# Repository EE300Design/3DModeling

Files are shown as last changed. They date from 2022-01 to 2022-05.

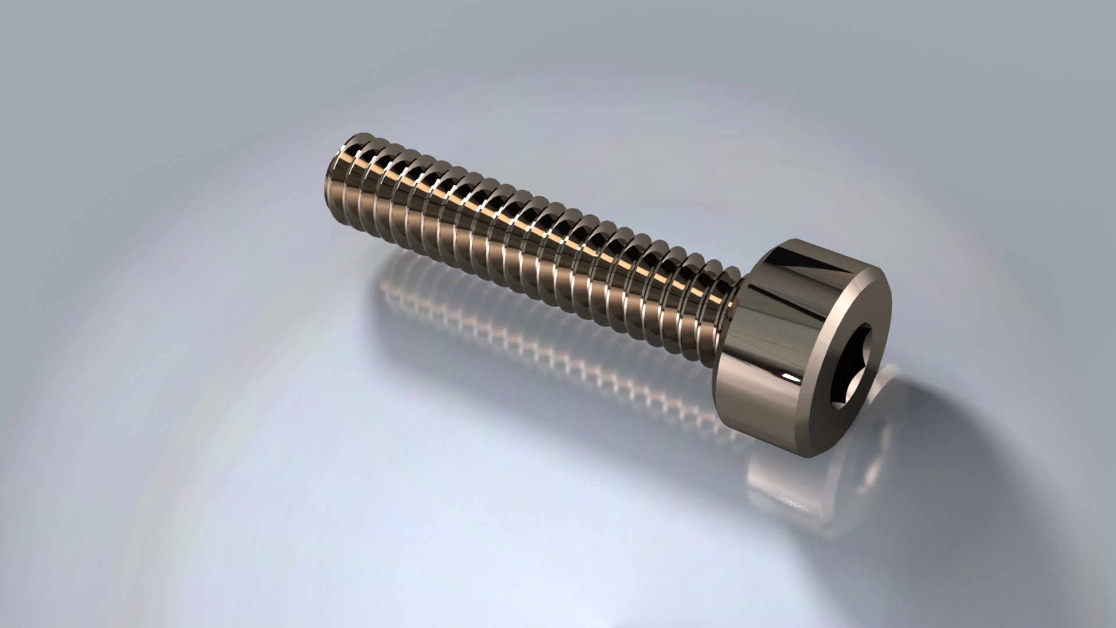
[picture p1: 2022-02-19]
Fusion_Model/Component_Models/M2_Metric_Screws/all-m2-sh-standard-screws-m2-hex-nut-and-flat-washer-for-m2-screw-1.snapshot.20/Metric Screw (3) 2.jpg

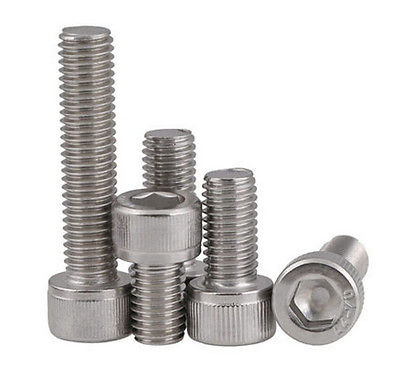
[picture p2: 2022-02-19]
Fusion_Model/Component_Models/M2_Metric_Screws/all-m2-sh-standard-screws-m2-hex-nut-and-flat-washer-for-m2-screw-1.snapshot.20/M2-M25-M3-316-A4-Stainless-Steel-Hex.jpg

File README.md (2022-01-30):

# 3DModeling
This is the working space for EE300 design project collaboration

## References
[1] https://lidarscanner.wordpress.com/2015/03/28/final-presentation/ \
[2] https://cdn.webshopapp.com/shops/304271/files/333438293/develop-routine-of-tf-luna-in-arduino.pdf \
[3] https://github.com/budryerson/TFLuna-I2C \
[4] https://youtu.be/diuOMDRtIMI \
[5] https://github.com/TravisLedo/LidarScanRender \
[6] https://create.arduino.cc/projecthub/TravisLedo/arduino-lidar-scanning-java-rendering-6b2124 \
[7] https://www.arduino.cc/reference/en/libraries/stepperdriver/ \
[8] https://www.youtube.com/watch?v=fHAO7SW-SZI

## Parts
| Component | Quantity | Purpose | Link | Cost($) |
| --- | --- | --- | --- | --- |
| `Nema17 Stepper Motor` | 1 | Drive Rotation Plate | https://www.amazon.com/dp/B07THK76QQ?psc=1&ref=ppx_yo2_dt_b_product_details | 10.99 |
| `Nema17 Stepper Motor 400mm thread` | 1 | Vertical Motion | https://www.amazon.com/dp/B07YQQGQ4C?psc=1&ref=ppx_yo2_dt_b_product_details | 35.99 |
| `450mm Linear Motion Rails` | 4 | Vertical Motion Support | https://www.amazon.com/dp/B08HWJVX63?psc=1&ref=ppx_yo2_dt_b_product_details | 35.98 |
| `12mm Linear Ball Bearing` | 4 | Vertical Motion | https://www.amazon.com/dp/B07H95FFP1?ref=ppx_yo2_dt_b_product_details&th=1 | 11.99 |
| `TF-Luna Lidar` | 1 | LIDAR | https://www.amazon.com/dp/B08F55QTWP?psc=1&ref=ppx_yo2_dt_b_product_details |25.98 |
| `A4988 Stepper Driver` | 5 | Stepper Driver | https://www.amazon.com/dp/B07BND65C8?psc=1&ref=ppx_yo2_dt_b_product_details | 9.69 |
| `Arduino Uno R3` | 1 | Micro-Controller | https://www.amazon.com/dp/B008GRTSV6?psc=1&ref=ppx_yo2_dt_b_product_details | 22.88 |
| `Nylon Spacer` | 320 | PCB Stand-off | https://www.amazon.com/dp/B008GRTSV6?psc=1&ref=ppx_yo2_dt_b_product_details | 11.88 |
| `M3 Threaded Inserts` | 120 | PCB Mounting | https://www.amazon.com/dp/B09KZSJS88?psc=1&ref=ppx_yo2_dt_b_product_details | 12.99 |
| `100uF Cap` | 20 | PCB | https://www.digikey.com/en/products/detail/kemet/ESK107M016AE3AA/13176338 | 3.42 | 
| `0.1uF Cap` | 20 | PCB | https://www.digikey.com/en/products/detail/w%C3%BCrth-elektronik/885012207045/5453900 | 1.12 |
| `TE 1x4 Connector`| 4 | PCB | https://www.digikey.com/en/products/detail/te-connectivity-amp-connectors/796949-4/2223910 | 8.12 |
| `PWR Jack` | 4 | PCB | https://www.digikey.com/en/products/detail/te-connectivity-amp-connectors/796949-4/2223910 | 2.76 |

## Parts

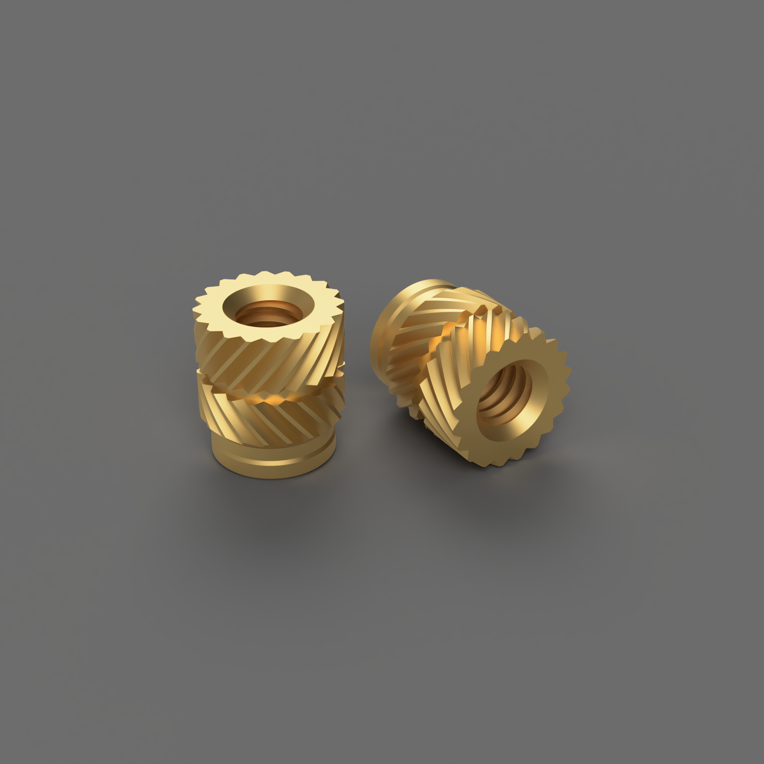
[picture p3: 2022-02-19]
Fusion_Model/Component_Models/M2_Threaded_Insert/threaded-insert-m2-x-4mm-for-3d-printed-parts-1.snapshot.5/08a98328-2d2f-4b6d-87d2-8571cb3f2b7b 2.PNG

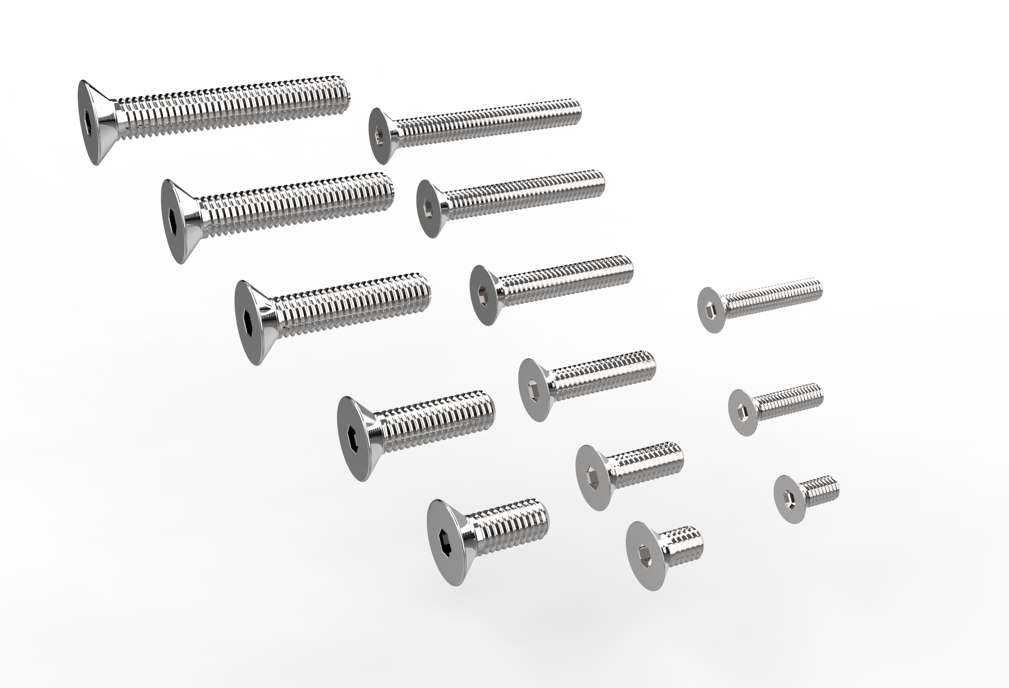
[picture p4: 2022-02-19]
Fusion_Model/Component_Models/Metric_Screws/All_Screws_M3_M4_M5/untitled.126.png

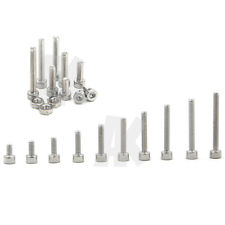
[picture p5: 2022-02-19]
Fusion_Model/Component_Models/M2_Metric_Screws/all-m2-sh-standard-screws-m2-hex-nut-and-flat-washer-for-m2-screw-1.snapshot.20/s-l225 2.jpg

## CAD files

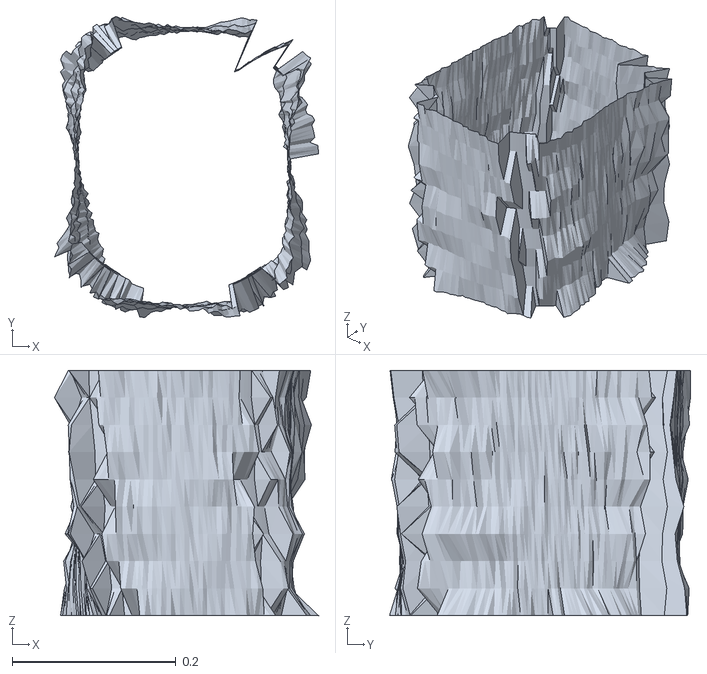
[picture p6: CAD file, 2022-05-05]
Application/Saved_examples/First_cube.stl
0.323 x 0.368 x 0.3

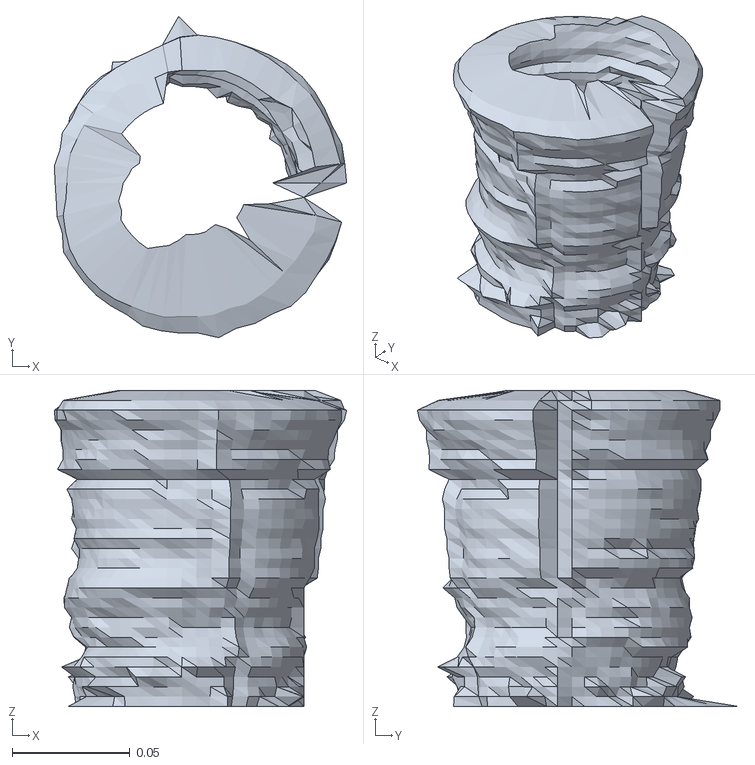
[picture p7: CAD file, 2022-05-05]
Application/test.stl
0.124 x 0.137 x 0.134

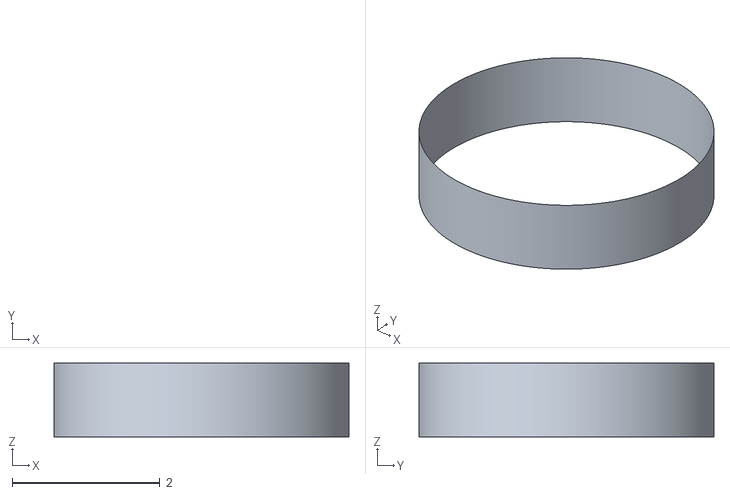
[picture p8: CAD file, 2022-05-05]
data_processing/test.stl
4.00 x 4.00 x 1.00

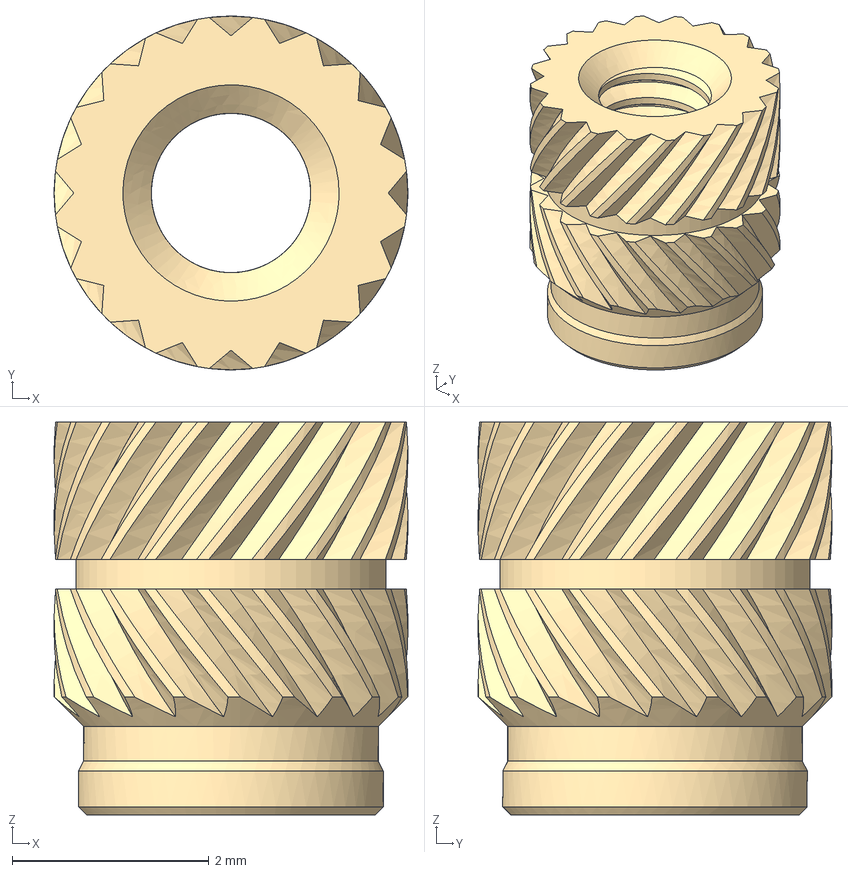
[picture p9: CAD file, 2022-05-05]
Fusion_Model/Component_Models/M2_Threaded_Insert/threaded-insert-m2-x-4mm-for-3d-printed-parts-1.snapshot.5/Threaded Insert M2 v1.iges
3.60 x 3.60 x 4.00 mm

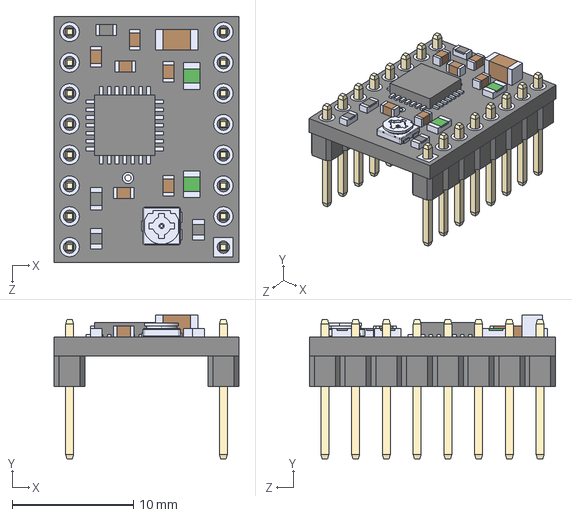
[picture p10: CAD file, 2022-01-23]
PCB_Design/Libraries&Footprints/A4988_Stepper_Driver/A4988_STEPPER_MOTOR_DRIVER_CARRIER.step
15.2 x 11.9 x 20.3 mm

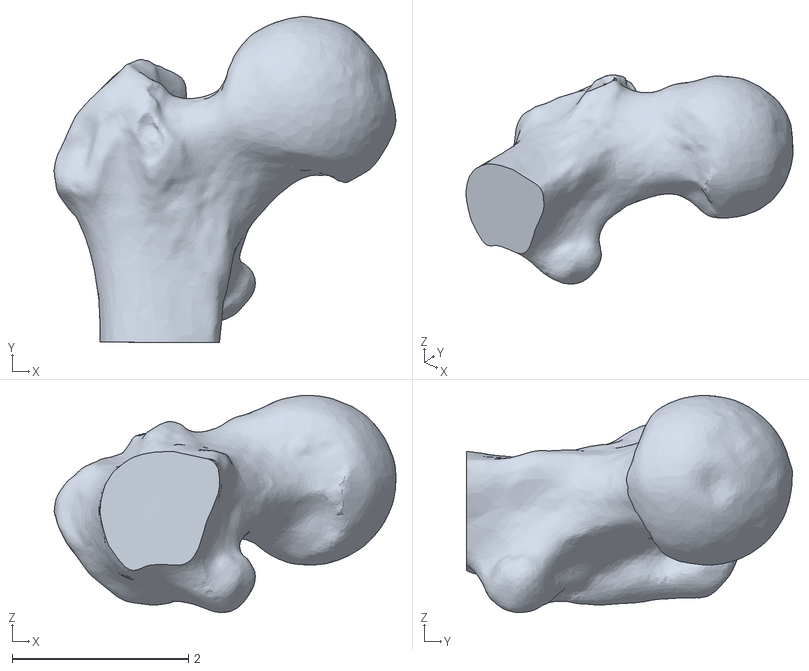
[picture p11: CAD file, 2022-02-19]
Application/femur.stl
3.87 x 3.70 x 2.46

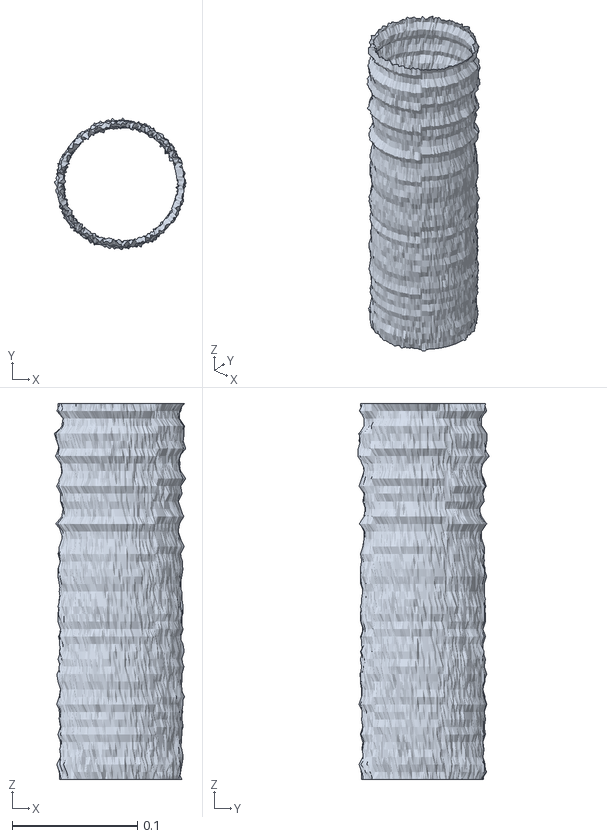
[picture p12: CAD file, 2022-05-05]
Application/Saved_examples/Oats_can.stl
0.105 x 0.105 x 0.3

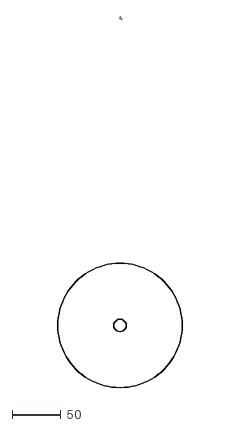
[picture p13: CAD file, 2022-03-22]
Fusion_Model/3D_STLS/Plate_DXF.dxf
128.0 x 382.2

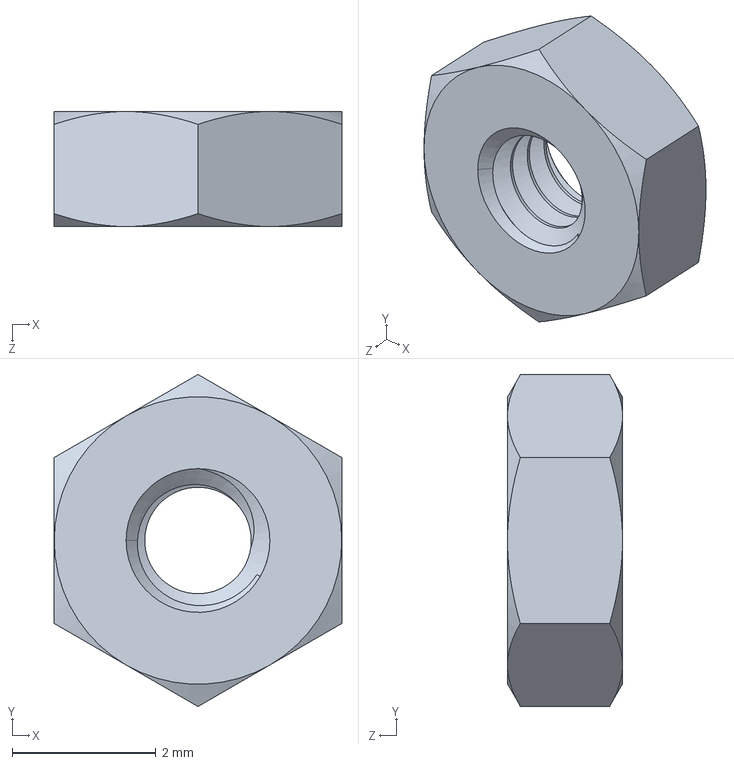
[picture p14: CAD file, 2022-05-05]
Fusion_Model/Component_Models/M2_Metric_Screws/all-m2-sh-standard-screws-m2-hex-nut-and-flat-washer-for-m2-screw-1.snapshot.20/M2 x 0.4mm Thread HEX NUT 2.STEP
4.00 x 4.62 x 1.60 mm

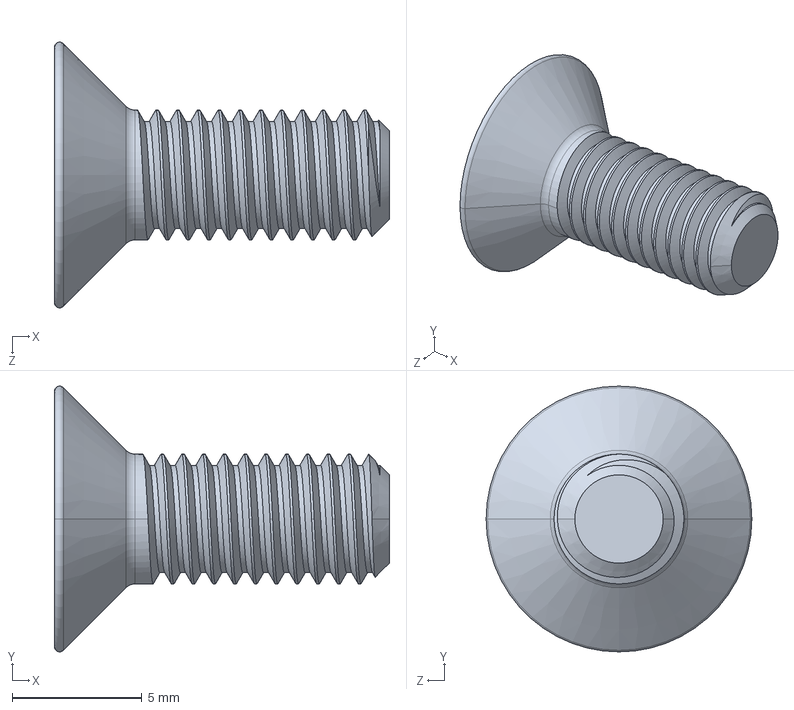
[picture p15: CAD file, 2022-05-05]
Fusion_Model/Component_Models/Metric_Screws/All_Screws_M3_M4_M5/M5_Countersunk_10 2.STEP
12.9 x 10.2 x 10.2 mm

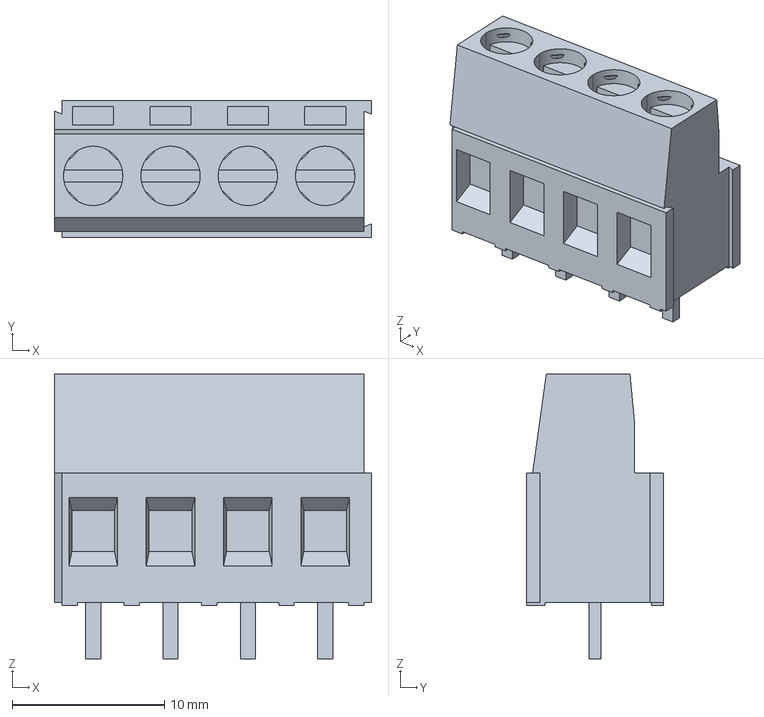
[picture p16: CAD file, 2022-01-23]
PCB_Design/Libraries&Footprints/TE_Terminal_Block/796949-4.step
20.8 x 9.00 x 18.7 mm

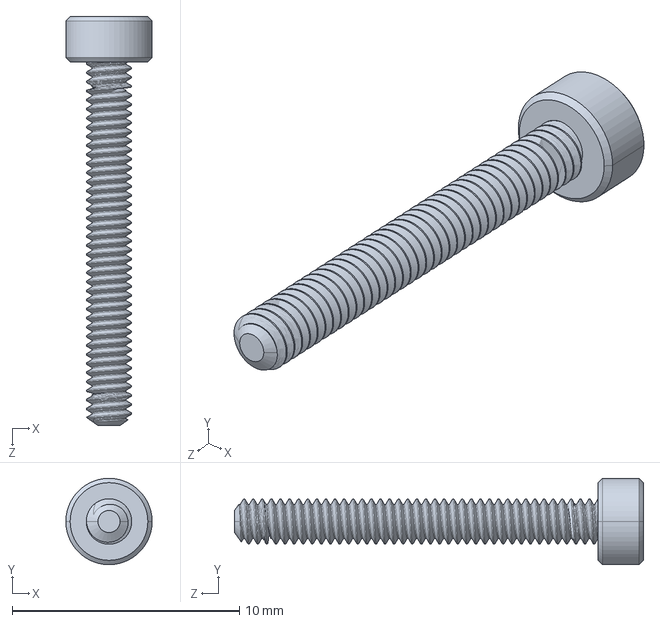
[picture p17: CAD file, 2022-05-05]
Fusion_Model/Component_Models/M2_Metric_Screws/all-m2-sh-standard-screws-m2-hex-nut-and-flat-washer-for-m2-screw-1.snapshot.20/M2 x 0.4mm Thread 16mm LONG SOCKET HEAD CAP SCREW.STEP
3.80 x 3.80 x 18.0 mm

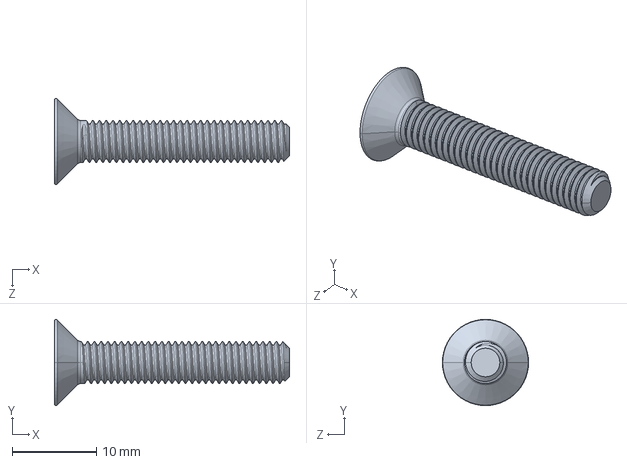
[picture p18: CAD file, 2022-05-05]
Fusion_Model/Component_Models/Metric_Screws/All_Screws_M3_M4_M5/M5_Countersunk_25 2.STEP
27.9 x 10.2 x 10.2 mm

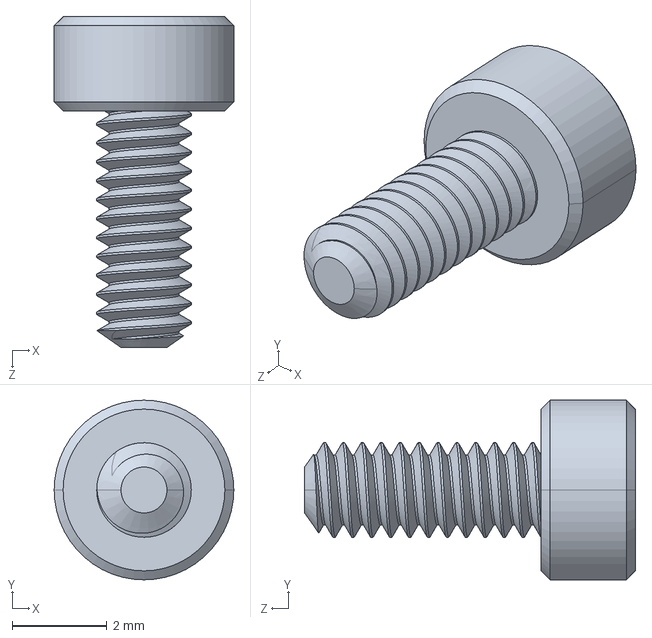
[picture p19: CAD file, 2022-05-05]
Fusion_Model/Component_Models/M2_Metric_Screws/all-m2-sh-standard-screws-m2-hex-nut-and-flat-washer-for-m2-screw-1.snapshot.20/M2 x 0.4mm Thread 5mm LONG SOCKET HEAD CAP SCREW.STEP
3.80 x 3.80 x 7.00 mm

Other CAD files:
Fusion_Model/3D_STLS/Plate_DXF_recover.dwg
Fusion_Model/Component_Models/Metric_Screws/All_Screws_M3_M4_M5/M4_Counter_sunk_20 2.STEP
Fusion_Model/Component_Models/M2_Metric_Screws/all-m2-sh-standard-screws-m2-hex-nut-and-flat-washer-for-m2-screw-1.snapshot.20/M2 x 0.4mm Thread 6mm LONG SOCKET HEAD CAP SCREW 2.STEP
Fusion_Model/Component_Models/M2_Metric_Screws/all-m2-sh-standard-screws-m2-hex-nut-and-flat-washer-for-m2-screw-1.snapshot.20/M2 screw size FLAT WASHER 2.STEP
Fusion_Model/Component_Models/M2_Metric_Screws/all-m2-sh-standard-screws-m2-hex-nut-and-flat-washer-for-m2-screw-1.snapshot.20/M2 screw size FLAT WASHER 2.x_t
Fusion_Model/Component_Models/M2_Metric_Screws/all-m2-sh-standard-screws-m2-hex-nut-and-flat-washer-for-m2-screw-1.snapshot.20/M2 screw size FLAT WASHER.STEP
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

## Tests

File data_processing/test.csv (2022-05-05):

2.000000000000000000e+00 | 2.000000000000000000e+00 | 2.000000000000000000e+00 | 2.000000000000000000e+00 | 2.000000000000000000e+00 | 2.000000000000000000e+00 | 2.000000000000000000e+00 | 2.000000000000000000e+00 | 2.000000000000000000e+00 | 2.000000000000000000e+00 | 2.000000000000000000e+00 | 2.000000000000000000e+00 | 2.000000000000000000e+00 | 2.000000000000000000e+00 | 2.000000000000000000e+00 | 2.000000000000000000e+00 | 2.000000000000000000e+00 | 2.000000000000000000e+00 | 2.000000000000000000e+00 | 2.000000000000000000e+00 | 2.000000000000000000e+00 | 2.000000000000000000e+00 | 2.000000000000000000e+00 | 2.000000000000000000e+00 | 2.000000000000000000e+00 | 2.000000000000000000e+00 | 2.000000000000000000e+00 | 2.000000000000000000e+00 | 2.000000000000000000e+00 | 2.000000000000000000e+00 | 2.000000000000000000e+00 | 2.000000000000000000e+00 | 2.000000000000000000e+00 | 2.000000000000000000e+00 | 2.000000000000000000e+00 | 2.000000000000000000e+00 | 2.000000000000000000e+00 | 2.000000000000000000e+00 | 2.000000000000000000e+00 | 2.000000000000000000e+00 | 2.000000000000000000e+00 | 2.000000000000000000e+00 | 2.000000000000000000e+00 | 2.000000000000000000e+00 |
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

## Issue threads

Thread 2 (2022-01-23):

Sourced Parts

LixianY, 2022-01-23:
Order the basic parts for the scanning platform construction.
These parts are :
1.Microcontroller:
https://www.amazon.com/Arduino-A000066-ARDUINO-UNO-R3/dp/B008GRTSV6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

2.Linear Rails for Stepper & Vertical Climb x4(450mm);
https://www.amazon.com/Linear-Motion-Hardened-Printer-Tolerance/dp/B08HWJVX63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

3.Nema17 Stepper Motor 400MM threaded:
https://www.amazon.com/Iverntech-Stepper-Integrated-Printers-Machine/dp/B07YQQGQ4C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

4.AR4988 Driver:
https://www.amazon.com/HiLetgo-Stepstick-Stepper-Printer-Compatible/dp/B07BND65C8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

5.LiDAR sensor:
https://www.amazon.com/gp/product/B088BBJ9SQ/ref=ox_sc_act_title_2?smid=AIJ7WJJN4HG6E&psc=1

Closed 2022-02-06.

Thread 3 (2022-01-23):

Search learning sources for 3D modeling

LixianY, 2022-01-23:
Find articles or blogs about:

1. Controlling the stepper motor.
2. Software platform for presenting 3D cloud dots collected by LiDAR sensors.
3. Needed mathetical tutorials, like coordinate transformation.

Closed 2022-04-23.

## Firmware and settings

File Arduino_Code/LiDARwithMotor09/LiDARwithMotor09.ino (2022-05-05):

#include <SoftwareSerial.h> //header file of software serial port
//The next line is commented as we are using mega
//SoftwareSerial Serial1(7,8); //define software serial port name as Serial1 and define pin7 as RX and pin8 as TX

//This version deals with limiting switches

/* For Arduino boards with multiple serial ports like DUEboard, interpret the above two pieces of code and directly use Serial1 serial port*/
int dist; //actual distance measurements of LiDAR 
int strength; //signal strength of LiDAR
float x_cor;
float y_cor;

//////////////////////////////
int check; //save check value
int i;
int uart[9]; //save data measured by LiDAR
const int HEADER=0x59; //frame header of data package 

// defines pins numbers
// Disk rotation motor
const int stepPin1 = 3; 
const int dirPin1 = 4; 
// Screw rotation motor
const int stepPin2 = 5; 
const int dirPin2 = 6; 
// Set up for limiting switches
const int LimSwitchUp = 8;
const int LimSwitchDw = 9;

const int heightIncrement = 80; // Height increment amount after one disk rotation


void setup() {
  Serial.begin(9600); //set bit rate of serial port connecting Arduino with computer
  Serial1.begin(115200); //set bit rate of serial port connecting LiDAR with Arduino 
    // For Stepper Motors, sets the four pins as Outputs
  pinMode(stepPin1,OUTPUT); // Disk rotation motor
  pinMode(dirPin1,OUTPUT);
  pinMode(stepPin2,OUTPUT); // Screw rotation motor
  pinMode(dirPin2,OUTPUT);
  pinMode(7,INPUT);// interrupt button
  pinMode(LimSwitchUp, INPUT);
  pinMode(LimSwitchDw, INPUT);
}


float heightData = 0;
int h = 0;
const int Length = 47; //sensor to the center of disk distance in cm


///////////////


void stop_scan(){
  digitalWrite(dirPin1,LOW); // Set the motor pins to a fixed value to stop them
  digitalWrite(stepPin1,HIGH); 
  digitalWrite(dirPin2,LOW); //
  digitalWrite(stepPin2,HIGH); 
  //digitalWrite(7,LOW);
  // Later, need to record the index where it stopped so that it can properly resume.
  
  }





void start_scan()//
{
  delay(100);
  bool exit_scan=false;
    //Set scanning max height limit 360 is found by 7200steps/20
  while(!exit_scan) {
    
    float theta = 0; // Angle of the disk rotation
    digitalWrite(dirPin1,LOW); // Enables the motor to move in a particular direction
    // Makes 200 pulses for making one full cycle rotation
    for(int x = 0; x < 200;) {
     int UpLim = digitalRead(LimSwitchUp);
     int DwLim = digitalRead(LimSwitchDw);
     int interrupt = digitalRead(7);
     
     if(interrupt == HIGH){
      
       stop_scan();
       digitalWrite(11,interrupt);
       exit_scan = true;
       break;
      }

      //Check if the upper limiting switch is pressed
      
      if(UpLim == HIGH){
        Serial.println("Move Down");
        digitalWrite(dirPin2,HIGH);
        
        //If pressed, rotates the carriage downward till initial position
        while(DwLim == LOW){
        DwLim = digitalRead(LimSwitchDw);
        digitalWrite(stepPin2,HIGH); 
        delayMicroseconds(500); 
        digitalWrite(stepPin2,LOW); 
        delayMicroseconds(500);
        }
        exit_scan = true;
        break;
        }
     
     if (Serial1.available()) { //check if serial port has data input
        if(Serial1.read() == HEADER) { //assess data package frame header 0x59 
          uart[0]=HEADER;
            if (Serial1.read() == HEADER) { //assess data package frame header 0x59
              uart[1] = HEADER;
              for (i = 2; i < 9; i++) { //save data in array
                uart[i] = Serial1.read(); 
                }
              check = uart[0] + uart[1] + uart[2] + uart[3] + uart[4] + uart[5] + uart[6] + uart[7]; 
              if (uart[8] == (check & 0xff)) { //verify the received data as per protocol
                dist = uart[2] + uart[3] * 256; //calculate distance value [mm]
                float cmdist = dist/10.0;  // convert to cm
                strength = uart[4] + uart[5] * 256; //calculate signal strength value 
          
                //Serial1.flush();
                delay(100);
                digitalWrite(stepPin1,HIGH); 
                delayMicroseconds(100); 
                digitalWrite(stepPin1,LOW); 
                delayMicroseconds(100);
                theta += 1.8;

                x++;
                // check if one full rotation completed
                if (x==200){
                  digitalWrite(dirPin2,LOW); // Enables the motor to move in clockwise direction
                                             // Makes 200 pulses for making one full cycle rotation
 
                  for(int x = 0; x < heightIncrement; x++) {
                      digitalWrite(stepPin2,HIGH); 
                      delayMicroseconds(500); 
                      digitalWrite(stepPin2,LOW); 
                      delayMicroseconds(500); 
                    }
    
                  h += heightIncrement; // counting height rotation steps
                  heightData = (heightData + h/26.7)/10; // calculate the hieght in cm
                  }

                // Perform coordinate conversion  
//                Serial.print(cmdist);
//                Serial.print(' ');
                x_cor = (Length-cmdist)*cos((theta/180) * 3.14159);
                y_cor = (Length-cmdist)*sin((theta/180) * 3.14159);
                Serial.print(x_cor); // output disk rotation angle
                Serial.print(' ');
                Serial.print(y_cor);
                Serial.print(' ');
                Serial.println(heightData);
               
                
          } 
         }
       }
    }
    else{
      Serial.println("No distance measured");
      }
    
      
  }
  
 }
 
}




//This version can take string sent from MATLAB and be reset by limiting switches
// Issues:
/*
 * The serial communication was not stable, scanning stops itself from time to time
 * Need to format the data, sending the distances only.
 * Need to avoid any racing conditions.
 */

void loop() {

    if (Serial.available() > 0) {
    // read the oldest byte in the serial buffer:
      
    int incomingByte = Serial.read();
    // if it's a capital H (ASCII 72), begin scanning
    if (incomingByte == 'H') {
      start_scan();
    }
    // if it's an L (ASCII 76) stops scanning
    if (incomingByte == 'L') {
      stop_scan();
    }
  }
    
 }

 

  
  

  
  








   

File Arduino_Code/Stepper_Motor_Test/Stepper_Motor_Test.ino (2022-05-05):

/*     Simple Stepper Motor Control Exaple Code
 */

// defines pins numbers
const int stepPin = 4; 
const int dirPin = 3; 
 
void setup() {
  // Sets the two pins as Outputs
  pinMode(stepPin,OUTPUT); 
  pinMode(dirPin,OUTPUT);
}
void loop() {
  digitalWrite(dirPin,LOW); // Enables the motor to move in a particular direction
  // Makes 200 pulses for making one full cycle rotation
  for(int x = 0; x < 200; x++) {
    digitalWrite(stepPin,HIGH); 
    delayMicroseconds(100); 
    digitalWrite(stepPin,LOW); 
    delayMicroseconds(50); 
  }
  delay(1000); // One second delay
  
//  digitalWrite(dirPin,LOW); //Changes the rotations direction
//  // Makes 400 pulses for making two full cycle rotation
//  for(int x = 0; x < 200; x++) {
//    digitalWrite(stepPin,HIGH);
//    delayMicroseconds(500);
//    digitalWrite(stepPin,LOW);
//    delayMicroseconds(500);
//  }
//  delay(1000);
}

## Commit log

2022-01-23 Added PCB design Folder
2022-01-23 Added KiCad MainBoard
    [Main_Board.kicad_pcb, Main_Board.sch]
2022-01-23 Added Folder for Libraries and Footprints
2022-01-23 Added Arduino Uno Libraries
2022-01-23 Added More Component Libraries
    [A4988_STEPPER_MOTOR_DRIVER_CARRIER.step]
2022-01-23 Added More Component Libraries & Footprints
2022-01-23 Schematic Complete
    [Main_Board.sch]
2022-01-23 Found some good resources in python to write STL files
2022-01-23 Added Terminal Libraries
    [796949-4.step, Main_Board.sch]
2022-01-23 Added Net List
    [Main_Board.sch]
2022-01-23 Cube STL python script
    [cube_demo.stl]
2022-01-24 Finilizing PCB Routing
    [Main_Board.kicad_pcb, Main_Board.sch]
2022-01-24 Added another version for MAC
    [Main_Board.kicad_pcb, Main_Board.sch, Main_Board_Ver2.kicad_pcb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]
2022-01-24 Fixed script to make viewable stl
    This is the example given on the numpy-stl documentation.
    [cube_demo.stl]
2022-01-24 Making Changes to MAC variant
    [Main_Board_Ver2.kicad_pcb]
2022-01-24 Finishing Power Lines
    [Main_Board_Ver2.kicad_pcb]
2022-01-25 PCB Final
    [Main_Board_Ver2.kicad_pcb, Main_Board_Ver2.kicad_sch]
2022-01-25 Final PCB
2022-01-25 Made script for generating cylinders
    Will be a good basis for transforming our measurements into STL files
    [cylinder_demo.stl]
2022-01-25 Update Cylinder_demo.stl
    The first one wasn't quite right.
    [cylinder_demo.stl]
2022-01-27 Model Folders
    [NEMA-17.312e5f25-d851-40d3-a168-f1d31e449f65.f3d]
2022-01-27 created cylinder generator that will be used for data and training
2022-01-27 Models Cont
    [T8 Screw nut.f3d, T8 Screw nut.step]
2022-01-28 Added T-Slot Aluminum Rails
    [20 X 20 mm Extrusion Sample Part MK1.step, TSlot-2020-Grooved.FCStd, TSlot-2020-Grooved.step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]
2022-01-28 Added Pillow Block Bearing
    [608RS.SLDPRT, KFL08.IGS, KFL08.SLDASM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]
2022-01-29 Added T-slot Mount and Nuts
    [2020 Corner Bracket STL.stl, Gusseted 2020 corner bracket v2.step, M5_T_Slot nut v2.step]
2022-01-29 Cleaned up script for generating cubes and cylinders
    Need to add comments, as well as filling the data/cube and data/cylinder with files of either csv's or stl files.
2022-01-29 Added 12mm Horizontal shaft Holder
    [SK12.SLDPRT]
2022-01-29 Added 12mm Linear vertical holders
    [SHF12.SLDPRT]
2022-01-29 Added Screws and Inserts
    [Insert Brass M5.ipt, M5x10.SLDPRT, M5x12.SLDPRT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]
2022-01-29 PCB Updates
    [Main_Board_Ver2-B_Cu.gbr, Main_Board_Ver2-B_Mask.gbr, Main_Board_Ver2-B_Paste.gbr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]
2022-01-29 Arduino Test COde
2022-01-29 Create Stepper motor test 1
2022-01-29 LiDAR demo
2022-01-30 Generated the cube and cylinder matrixes.
    The saved files are 2D matrixes of randomized cubes and cylinder matrixes. The height is normalized, so the data is irregardless of the row index. The column index linearly maps to 2 pi radians.
    [Main_Board_Ver2-B_Cu.gbr, Main_Board_Ver2-B_Mask.gbr, Main_Board_Ver2-B_Paste.gbr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]
2022-01-31 Code for combining all tree coordinates
    Attempted to combine motor data (angle and height) with LiDAR distance data readings.
2022-02-02 A sample 3D model data for testing
    [bun_zipper.ply]
2022-02-02 Added Limit Switch Model
    [Fim de Curso - KW12-3.f3d, Fim de Curso - KW12-3.stp]
2022-02-03 Finally got the image data to work and it makes sense
    [cube0.csv, cube1.csv, cube10.csv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]
2022-02-04 Demo'd classifying cube and cylinders
2022-02-06 Model Updates
    [Fim de Curso - KW12-3.f3d, Fim de Curso - KW12-3.stp, LIDAR_Carrage v4.f3z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]
2022-02-06 Added DXF's
    [Base_1 v19.stl, LIDAR_Carrage v3.stl, Limit_Switch_Mount v3.stl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]
2022-02-14 Updating data
    [cube_demo.stl, cylinder_demo.stl, test.stl]
2022-02-16 Made serial communication with python
    used serial communication to collect data from Arduino and write to a txt file
2022-02-17 Communication for LiDAR Arduino code
2022-02-17 Added Additional Models
    [M2 screw size FLAT WASHER.STEP, M2 screw size FLAT WASHER.x_t, M2 x 0.4mm Thread 10mm LONG SOCKET HEAD CAP SCREW.IGS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]
2022-02-19 updated the app
    [cube.stl, cylinder.stl, femur.stl]
2022-02-19 Update to the app
    [M2 screw size FLAT WASHER.STEP, M2 screw size FLAT WASHER.x_t, M2 x 0.4mm Thread HEX NUT.IGS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]
2022-02-19 Updated Arduino code with coordinate conversion to xyz
    [M2 screw size FLAT WASHER 2.STEP, M2 screw size FLAT WASHER 2.x_t, M2 x 0.4mm Thread 10mm LONG SOCKET HEAD CAP SCREW 2.IGS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]
2022-02-20 Added DXF for plate
    [Plate_DXF.dxf, Plate_DXF_recover.dwg]
2022-02-21 Fixed one bug in Arduino (avoid conflicting variables)
    There was a coordinate x and a counting x variables conflicting
    [LiDARwithMotor03.ino]
2022-03-03 filtered old generated data
2022-03-22 update data
    update
    [20 X 20 mm Extrusion Sample Part MK1.step, 2020 Corner Bracket STL.stl, 608RS.SLDPRT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]
2022-03-22 Commenting Arduino Code
    [bun_zipper.ply]
2022-03-28 Tested Arduino Interrupt and Real time plot in MATLAB
2022-04-06 print data line by line
2022-04-10 Limiting switches for resetting carriage positions
    [LiDARwithMotor09.ino, LiDARwithMotor10.ino]
2022-04-22 Updated unit calibration and serial echo with GUI
2022-04-23 Modified to adapt to Arduino protenta
2022-04-23 Scanned samples
2022-04-25 Reset and Reposition added
    [LiDARwithMotor13.ino]
2022-05-05 Update 5/5
    [cube.stl, cylinder.stl, femur.stl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]
2022-05-05 Updated /application to current version
    [First_cube.stl, Oats_can.stl, data_x_x2_x3.csv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]
